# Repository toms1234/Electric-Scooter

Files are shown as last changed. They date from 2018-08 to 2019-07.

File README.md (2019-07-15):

# Electric-Scooter
////////////////////////////////////////////////////////////////////////////////////////////////////////////////////////////////////////
### TO-DO List
- [x] STAY UP TO DATE WITH THE COSTS OF THIS PROJECT
- [x] Add mathematics program output image (mathematics.jpg)
- [x] Add the Inventor Assembly as an image (design.gif & design.stl)
- [ ] Add an image of the mechanical part finished (mechanical.jpg)
- [ ] Add images of implemented safety (emergency stop & wiring in waterproof box = safety1.jpg & safety2.jpg)
- [ ] Add top speed in km/h and mph
- [ ] Add cost price
- [ ] Add logs (August 2018 up to ???)
- [ ] Add a complete image (final.jpg)
- [ ] Add a video demonstration (youtube video)
- [ ] Remove this list (everything in between the slashes)

////////////////////////////////////////////////////////////////////////////////////////////////////////////////////////////////////////


Top speed: ??? km/h ≈ ??? mph. [Video demonstration](http://www.youtube.com/watch?v=).

## The Idea
A design and practical implementation of a three-phase brushless DC (BLDC) motor control system for an electric scooter. 

My goal is to create an electric scooter that is powerful enough to pull me up hills while still keeping my own (and of course other road users) safety in mind. In this project I will address several possibilities to make the scooter safer.

The choices I made about the parts are discussed and compared with other possibilities.

The problems I faced during this project and how I fixed these problems are also discussed and explained. I also made a cost price of my scooter and compared it to current market offers of electric scooters.

## The Process
### 1. Risks
Some of the risks I thought of:
* Motor cannot be stopped
* Insufficient braking capacity
* Mass inertia
* Possible danger of understeer
* Too fast/estimation problem due to environment
* Too fast/estimation problem due to driver
* Not being able to warn other road users
* Accelerate too fast/decelerate too slowly
* Poor lighting
* Controller defective (throttle)
* Fall hazard due to driving with one hand
* Fall hazard due to not sitting on a saddle
* Risk of clamping of limbs/clothing
* Danger of slipping due to combination tire-road surface
* Explosion of the tires due to high speed
* Too large of a reaction time during braking
* Overheating of the motor
* Overheating the speedcontroller
* Possible dangers of the battery
* Short-circuit due to water intrusion/sudden temperature changes
* Slipping over footplate
* Hazards due to imbalance of the vehicle
* Uncontrollability during testing
* Roller chain fails

### 2. Mathematics
Took me less than 10 mins to write this simple mathematics program which will give me an easier time choosing a gear ratio:
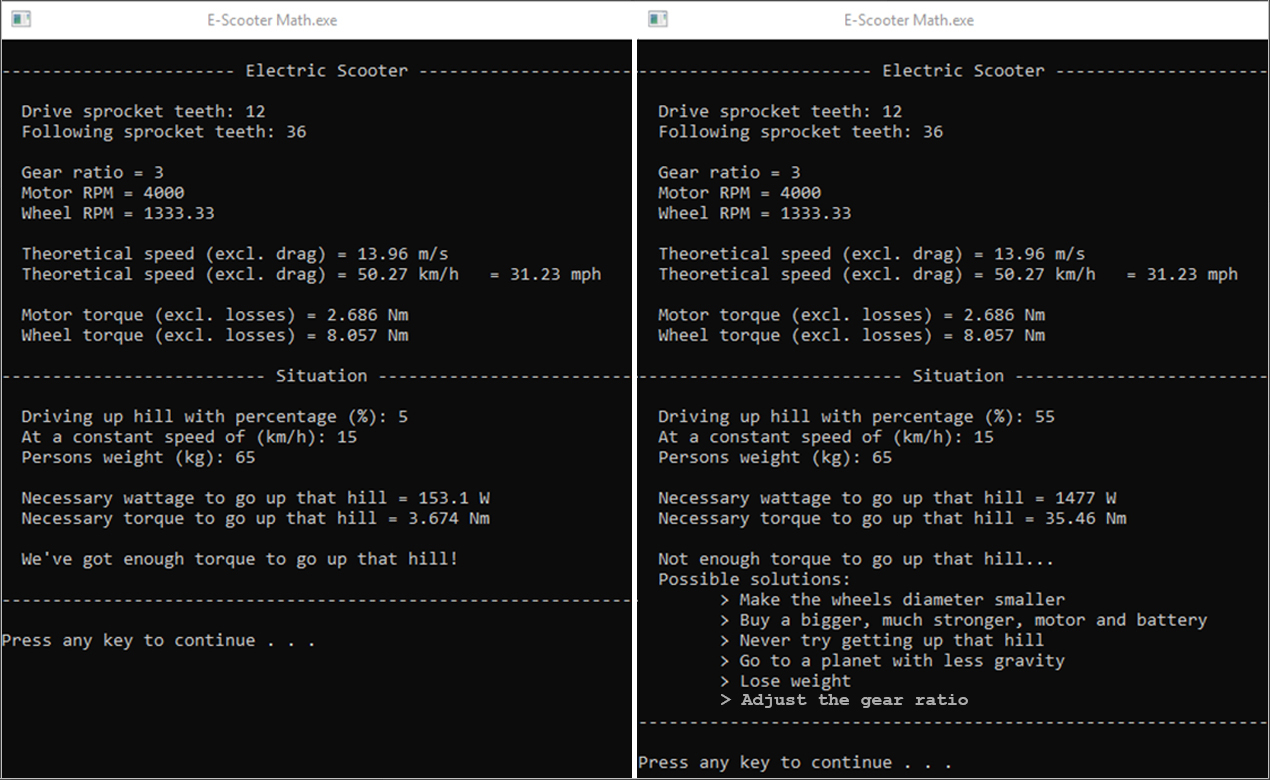
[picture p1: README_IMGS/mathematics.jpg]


The code is in the source. I later realised I could've simply used Excel...

As seen in the above (left) console output a gear ratio of 12 to 36 would do fine. I chose to go with the following parts:
* Drive sprocket (12 tooth 3/8“ x 7/32“ DIN ISO 606)
* Driven sprocket (36 tooth 3/8“ x 7/32“ DIN ISO 606)
* Roller chain (3/8“ x 7/32“ DIN ISO 606)

### 3. Design
I'm designing a completely new scooter frame, based of casual scooters with the motor driving the rear wheel.



Main electronics. These will go inside the waterproof box:
* Turnigy Aerodrive SK3 - 6374-149KV Brushless Outrunner Motor
* YEP 120A HV (4~14S) Brushless Speed Controller (OPTO)
* ZIPPY Compact 5000mAh 6S 25C Lipo Pack
* Arduino Uno V3

I chose to go with the above electronic components simply because I had already bought these for my [electric bike](https://github.com/rubenvanopstal/Electric-Bike) which I had disassembled before starting this project.

### 4. Production
Processes used to fabricate the scooter:
* Welding
* Milling
* Turning
* Boring
* Tapping



### 5. Software
First code, needs safety implementation:
```C++
#include <Servo.h>
Servo esc;

int throttlePin = 0;
 
void setup(){
  esc.attach(8);
}
 
void loop(){
  int throttle = analogRead(throttlePin);
  throttle = map(throttle, 0, 1023, 0, 179);
  esc.write(throttle);
}
```

### 6. Safety
Applying safety by thinking back on the risks I talked about. Changing software/hardware:
* Added a waterproof box (Short-circuit due to water intrusion/sudden temperature changes)
* Added an emergency stop (Motor cannot be stopped)
* Added a main switch
* Added fuses




* Added ramping in my code (Accelerate too fast/decelerate too slowly)
```C++
#include <Servo.h>
Servo esc;

#define throttlePin A0

#define MIN_READ_VALUE 178
#define MAX_READ_VALUE 880
#define MAX_SETPOINT 700
#define MAX_PWM 180

float throttleValue, throttleSafe, speed_diff, acceleration, setpoint, pwmCalc;

void setup() {
  pinMode(throttlePin, INPUT);
  esc.attach(8);
}

void loop() {  
  throttleValue = analogRead(throttlePin);
  if ((throttleValue > (MIN_READ_VALUE - 60)) && (throttleValue < (MAX_READ_VALUE + 20)))
  {    
    setpoint = throttleValue - 176;
    if (abs(setpoint) < 4) {
      setpoint = 0;
    } else if (abs(setpoint) > 695) {
      setpoint = 695;
    }

    throttleSafe = (setpoint * MAX_PWM)/MAX_SETPOINT;
    speed_diff = setpoint - pwmCalc;

    if (speed_diff > 2) {
      acceleration += 2;
      delay(50);
    }
    if (speed_diff < -2) {
      acceleration -= 2;
    }
    if (acceleration > 178) {
      acceleration = 178;
    }
    if (acceleration < 0) {
      acceleration = 0;
    }
    
    pwmCalc = (acceleration * MAX_SETPOINT)/MAX_PWM;
    esc.write(acceleration);
  }
  else if (throttleValue < (MIN_READ_VALUE - 80))
  {
    esc.write(0);
  }
  else if (throttleValue > (MAX_READ_VALUE + 40))
  {
    esc.write(0);
  }
  
}
```

### 7. Pricing
Cost: **€ ???**
* Motor
* Speedcontroller
* Programming card
* Batteries (5S & 6S LiPo)
* LiPo Balance charger
* Scooter wheels (200mm x 50mm = 8“)
* Sprockets (12 tooth & 36 tooth 3/8“ x 7/32“ DIN ISO 606)
* Roller chain (3/8“ x 7/32“ DIN ISO 606)
* Translock/taperlock (8mm x 19mm)
* Steel for the frame
* Waterproof box
* Heat shrink tubing
* All sorts of connectors
* Fuses & fuse holder
* Main switch
* Cables

Expenses I didn't take into account:
* Cutting plates from the milling and turning process
* Welding wire, power consumption and gas consumption from the welding process
* Power consumption of the milling machine and lathe
* DC-to-DC step-down converter, wires, soldering, small fuse, resistors, ...

### 8. Logs
August 2018 up to ?????.

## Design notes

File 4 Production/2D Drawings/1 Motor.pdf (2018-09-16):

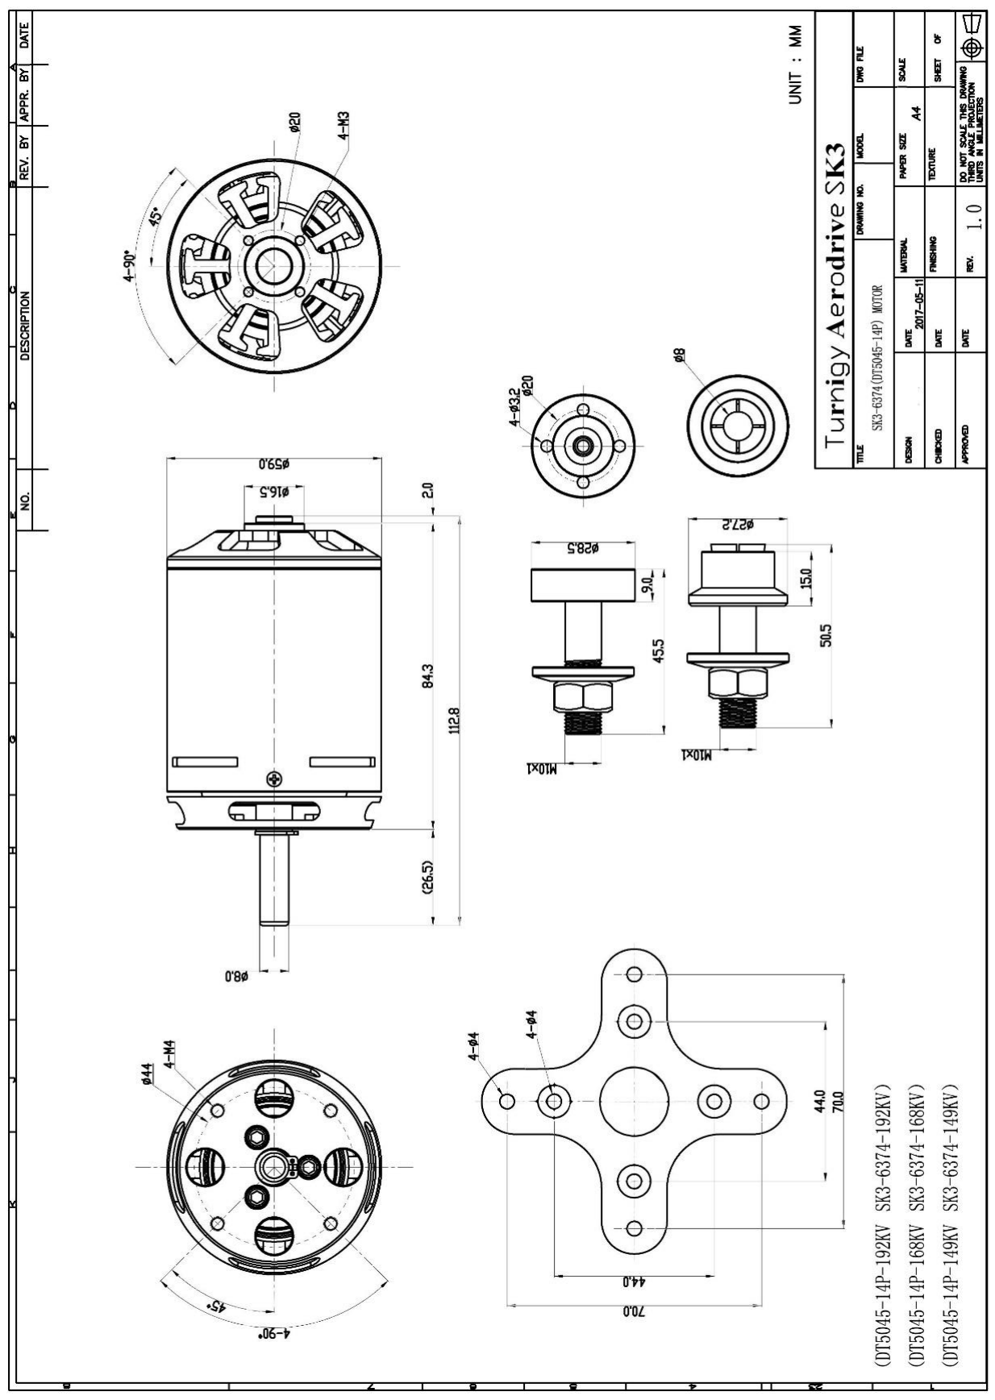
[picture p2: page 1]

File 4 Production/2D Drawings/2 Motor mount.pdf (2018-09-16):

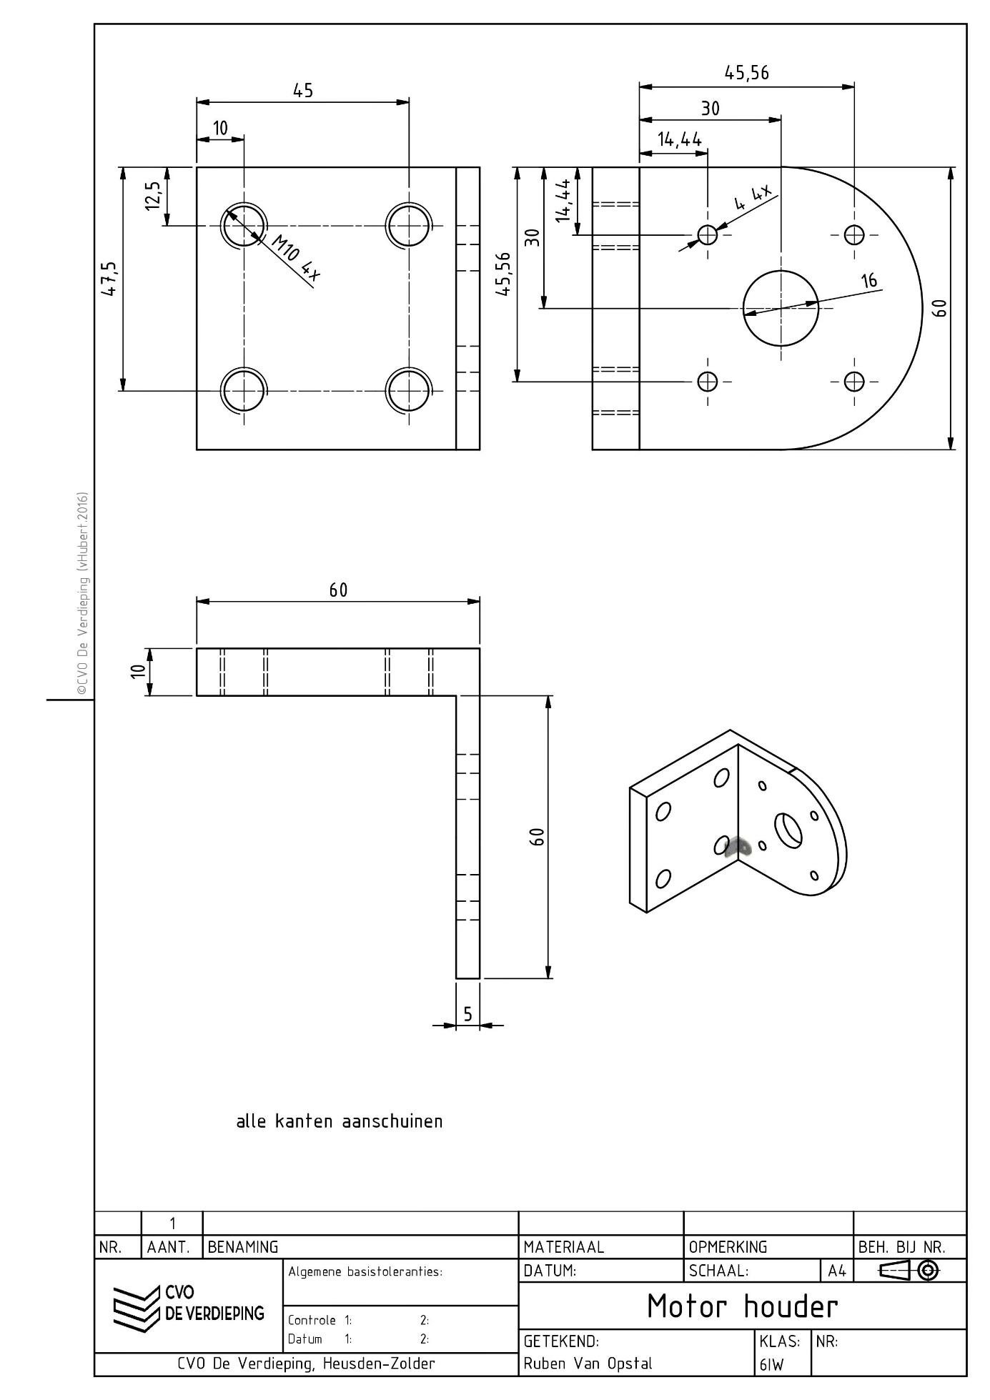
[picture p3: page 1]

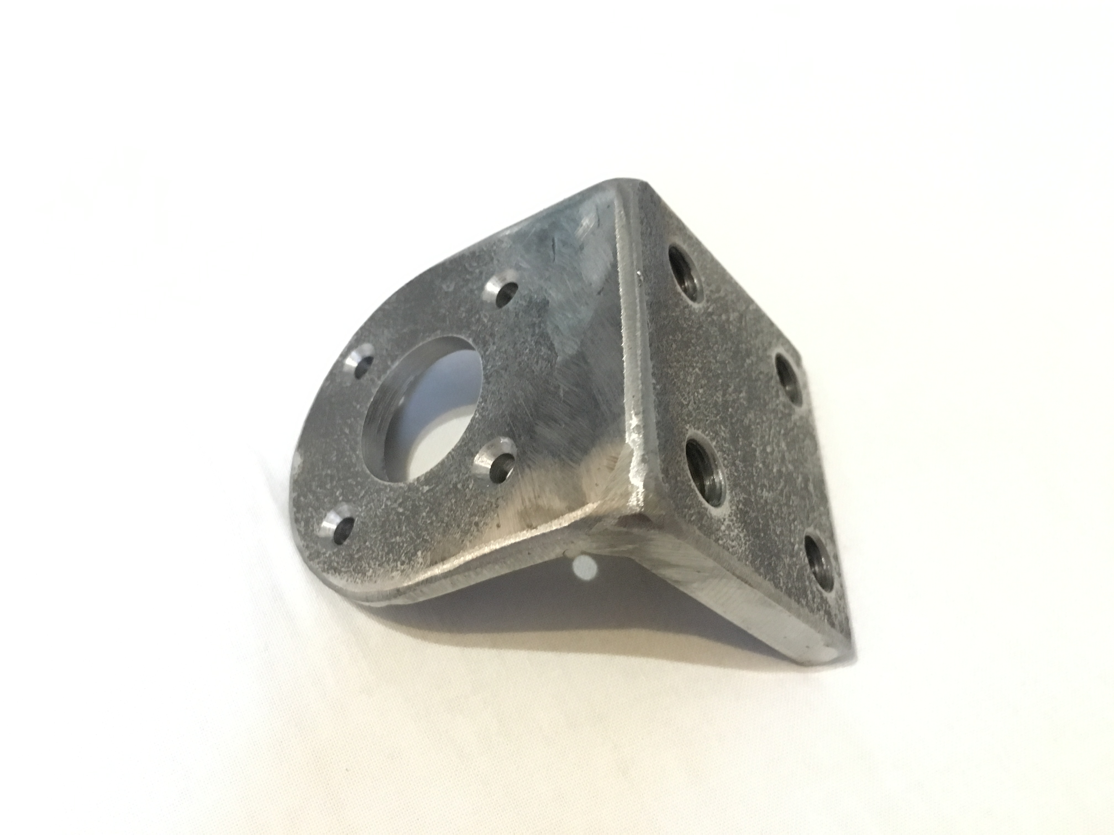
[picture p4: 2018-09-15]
4 Production/Pictures/3 Motor mount.JPG

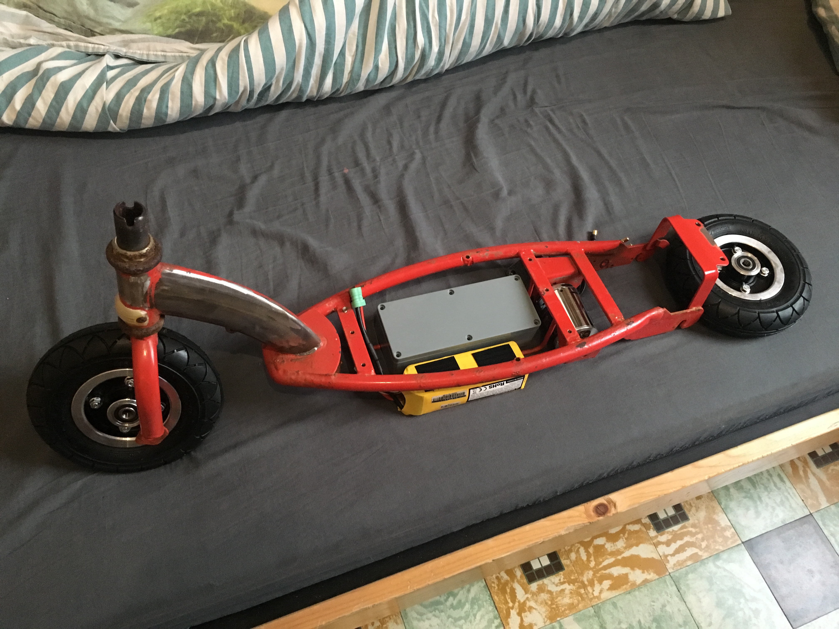
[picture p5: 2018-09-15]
4 Production/Pictures/1 Main idea.JPG

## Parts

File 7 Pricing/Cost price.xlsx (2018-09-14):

Cost price
Component | Type | Quantity | €/piece | Total
Electronics
Connectors | Team Corally - Bullit plug 6.5mm - Male | 2 | 6.50 | 13.00
Connectors | Team Corally - Bullit plug 6.5mm - Female | 2 | 6.50 | 13.00
Cables | Team Corally - Ultra V - Black and Red - 10AWG - ODø 5.5mm - 2x 1m | 2 | 19.95 | 39.90
Motor | Turnigy Aerodrive SK3 - 6374-149KV Brushless Outrunner Motor | 1 | 69.07 | 69.07
Speedcontroller | HobbyKing YEP 120A HV (4 ~ 14S) Brushless Speed Controller (OPTO) | 1 | 107.76 | 107.76
Programming card | YEP ESC Programming Card | 1 | 5.48 | 5.48
Battery | ZIPPY Compact 5000mAh 5S 25C Lipo Pack | 1 | 41.09 | 41.09
Battery | ZIPPY Compact 5000mAh 6S 25C Lipo Pack | 1 | 46.35 | 46.35
Battery charger | IMAX B6AC V2 Professional Balance Charger/Discharger | 1 | 38.19 | 38.19
Transmission
Sprocket | 12 tooth - 3/8“ x 7/32“ DIN ISO 606 | 2 | 2.93 | 5.86
Sprocket | 36 tooth - 3/8“ x 7/32“ DIN ISO 606 | 1 | 13.20 | 13.20
Roller chain | 3/8“ x 7/32“ DIN ISO 606 - 1m | 5 | 14.43 | 72.15
Connecting link | 3/8“ x 7/32“ DIN 8187 | 5 | 2.28 | 11.40
Taperlock | Translock® Mini - TRMINI8X19 - 8mm bore | 1 | 12.25 | 12.25
Wheels /w rims | 8“ - 200 x 50mm - Scoot wheels - Aluminium rims | 2 | 20.49 | 40.98
Aluminium / steel
 |  | 1 | 0.00 | 0.00
 |  | 1 | 0.00 | 0.00
 |  | 1 | 0.00 | 0.00
 |  | 1 | 0.00 | 0.00
 |  | 1 | 0.00 | 0.00
Safety
Case / box | Waterproof ABS box - Dark grey - 195 x 80 x 55mm G353 | 1 | 24.43 | 24.43
Cable shoes | Ring cable shoes - YELLOW - 6mm^2 - Diameter 8.4mm | 1 | 2.75 | 2.75
Cable shoes | Ring cable shoes - YELLOW - 6mm^2 - Diameter 6.4mm | 1 | 2.59 | 2.59
Fuse holder | Fuse holder for maxiOTO fuses | 1 | 11.39 | 11.39
Fuses | Blister maxiOTO fuses | 1 | 8.41 | 8.41
Main witch | Main switch 500A | 1 | 10.38 | 10.38
Griptape | SK8DLX Griptape | 1 | FREE | FREE
Totale kostprijs (€) | 589.63

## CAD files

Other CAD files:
3 Design/!Library/76229192-9-roulement_6000_2/OldVersions/roulement_6000_2.0003.iam
3 Design/!Library/76229192-9-roulement_6000_2/OldVersions/roulement_6000_2_01.0001.ipt
3 Design/!Library/76229192-9-roulement_6000_2/OldVersions/roulement_6000_2_02.0001.ipt
3 Design/!Library/76229192-9-roulement_6000_2/OldVersions/roulement_6000_2_03.0001.ipt
3 Design/!Library/76229192-9-roulement_6000_2/roulement_6000_2.iam
3 Design/!Library/76229192-9-roulement_6000_2/roulement_6000_2_01.ipt
3 Design/!Library/76229192-9-roulement_6000_2/roulement_6000_2_02.ipt
3 Design/!Library/76229192-9-roulement_6000_2/roulement_6000_2_03.ipt
3 Design/Electric-Scooter.iam
3 Design/Frame/Batterybox 1/Batterybox 1.ipt
3 Design/Frame/Batterybox 1/Waterproof box 1.ipt
3 Design/Frame/Batterybox 2/Batterybox 2.ipt
3 Design/Frame/Batterybox 2/OldVersions/Waterproof box 2.0008.ipt
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

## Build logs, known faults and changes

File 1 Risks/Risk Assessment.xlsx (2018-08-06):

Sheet: Revisie overzicht
Risico Analyse ombouwen tot electrisch aangedreven fiets
Revisie nummer | Omschrijving van de wijzigingen | Opgemaakt door / aanwezig tijdens meeting
1 | Opstart risico analyse, definitie, invullen, | Ruben Van Opstal / Maarten Wouters / Noach Van Opstal

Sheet: Risico Analyse
Risico Assessment Electric-Scooter
 | Risico Assessment |  | Evalution |  |  |  | Precautions and control measures
 | Actions of the involved people | Nature and description of the risks / problems | P | E | S | R | Source approach | Collective protection | Personal protection | Education | Instructions | Medical checkup | Other
item | Normal proceedings |  |  |  |  |  | Normal proceedings
1 | Motor cannot be stopped | Fall hazard, possible accident with other road users | 3 | 10 | 15 | 450 | Emergency stop | Warn bystanders | Protective clothing |  | Instruction card |  | Annual inspection of the complete vehicle by an authorized person with the necessary training
2 | Insufficient braking capacity | Not being able to stop in time, longer braking distance, swerve still possible | 1 | 6 | 7 | 42 | Better brakes or brake discs | Warn bystanders | Protective clothing
3 | Mass inertia | Heavier vehicle --> possible estimation problem with brakes | 6 | 10 | 15 | 900 |  |  | Protective clothing | Gain experience on private property | Instruction card
4 | Possible danger of understeer | By the electric drive relative to an ordinary vehicle | 0.5 | 3 | 3 | 4.5 |  |  | Protective clothing | Gain experience on private property | Instruction card
5 | Too fast / estimation problem due to environment | Danger to other road users | 3 | 6 | 7 | 126 | Limiter |  |  | Gain experience on private property
6 | Too fast / estimation problem due to driver | Danger to other road users + own danger | 6 | 10 | 15 | 900 | Limiter |  | Protective clothing | Gain experience on private property | Instruction card
7 | Not being able to warn other road users | Poor audible hearing possible by bystanders | 6 | 2 | 1 | 12 | A horn that mees certain conditions
8 | Accelerate too fast / decelrate too slowly | Lost vehicle control | 10 | 10 | 3 | 300 | Limiter |  | Protective clothing | Gain experience on private property | Instruction card
9 | Poor lighting | Invisible to other road users | 6 | 3 | 3 | 54 | Better lighting
10 | Controller defective (throttle) | Fall hazard, possible accident with other road users | 6 | 10 | 15 | 900 | Emergency stop |  | Protective clothing |  | Instruction card
11 | Fall hazard due to driving with one hand | Own danger | 3 | 1 | 7 | 21 | Manual, sensor that requires you to keep both hands on the handle bars |  | Protective clothing |  | Instruction card
12 | Fall hazard due to not sitting on a saddle | Own danger | 0.5 | 1 | 7 | 3.5 | Manual, add a saddle, sensor that requires you to sit on the saddle |  | Protective clothing |  | Instruction card
14 | Risk of clamping of limbs / clothing | Own danger | 6 | 10 | 7 | 420 | Hide objects with a pinch hazard |  | Protective clothing |  | Instruction card
15 | Danger of slipping due to combination tire-road surface | Lost vehicle control | 3 | 3 | 7 | 63 |  |  | Protective clothing | Gain experience on private property | Instruction card
16 | Explosion of tyres due to high speed | Lost vehicle control | 0.5 | 3 | 7 | 10.5 | Emergency stop, limiter |  | Protective clothing |  | Instruction card
18 | Too long of a reaction time during breaking | Danger to other road users + own danger | 6 | 10 | 3 | 180 |  | Warn bystanders | Protective clothing | Gain experience on private property | Instruction card
19 | Overheating of the motor | Technical failure of the vehicle | 0.5 | 10 | 1 | 5 | Cooling of the engine |  |  |  | Instruction card
20 | Overheating of the speedcontroller | Technical failure of the vehicle | 0.5 | 10 | 1 | 5 | Cooling of the speedcontroller |  |  |  | Instruction card
21 | Possible dangers of the battery | Explosion hazard, flammable | 3 | 6 | 1 | 18 | Protect the battery |  |  |  | Instruction card
22 | Short-circuit due to water intrusion / sudden temperature changes | Technical failure of the vehicle | 3 | 6 | 1 | 18 | Waterproofing of components |  |  |  | Instruction card
23 | Slipping over footplate | Fall hazard, possible accident with other road users | 3 | 1 | 1 | 3 | Griptape |  | Protective clothing
24 | Hazards due to imbalance of the vehicle | Fall hazard, possible accident with other road users | 10 | 10 | 3 | 300 | Counterweight |  | Protective clothing |  | Instruction card
25 | Roller chain fails | Technical failure of the vehicle | 0.2 | 10 | 1 | 2
27 | Uncontrollability during testing | Lost vehicle control | 10 | 10 | 15 | 1500 | Emergency stop | Testing in a controlled environment | Protective clothing | Gain experience on private property

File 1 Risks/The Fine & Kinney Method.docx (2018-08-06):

The Fine & Kinney Method
Probability (mathematical chance an incident will occur) | | | P
To be expected | | | 10
Possible | | | 6
Unusual (but possible) | | | 3
Unlikely, but possible in the long term | | | 1
Highly unlikely, but conceivable | | | 0,5
Almost unimaginable | | | 0,2
Next to impossible / unthinkable | | | 0,1
Exposure (duration that a risk can occur) | | | E
Constantly | 20-40 hrs/week (constantly) | | 10
Frequently | 10-20 hrs/week (1x/day) | | 6
Occasionally | 5-10 hrs/week (1x/week) | | 3
Sometimes | 2-5 hrs/week (1x/month) | | 2
Rarely | 10min-2hrs/week (2-3x/year) | | 1
Very rarely | < 10min/week. (1x/year) | | 0,5
Severity (possible damage, effects and consequences) | | | S
Disaster | Multiple dead people | | 100
Catastrophe | One or more dead people | | 40
Very severe | Fatal casualty | | 15
Severe | Lasting injury with absence | | 7
Important | Injury with absence (> several days but < months) | | 3
Slight effect | Injury without absence through illness | | 1
Risk-index (R) | Priority (P) | Risk = P * E * S
> 400 | 1 | Risk is too high; stop activities / operations
201-400 | 2 | High risk; apply large measures immediately
71-200 | 3 | Moderate risk; apply simple measures
21-70 | 4 | Little risk; attention required
0-20 | 5 | Slight risk; acceptable

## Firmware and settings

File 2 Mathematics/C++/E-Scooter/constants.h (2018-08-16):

#pragma once

#define M_PI 3.14159265358979323846264338327950288

const double batteryVolt = (6 * ((4.2 + 3.7) / 2));
const int motorRPM = 4000;		// at half voltage = 6S
const int motorWatt = 1125;		// watts

const double wheelDia = 0.2;	// meters

const double kmh_mph_ratio = 0.6213712;

const double gravity = 9.81;		// m/s^2
const double scooterWeight = 10;	// kg

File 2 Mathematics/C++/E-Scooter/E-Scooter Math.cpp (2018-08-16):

// Electric-Scooter-Mathematics.cpp : Defines the entry point for the console application.
//

#include "stdafx.h"
#include <iostream>
#include <iomanip>
#include <math.h>

int getInteger()
{
	while (true)
	{
		int x;
		std::cin >> x;
		std::cin.ignore(32767, '\n');

		if (std::cin.fail())
		{
			std::cin.clear();
			std::cin.ignore(32767, '\n');
		}
		else
			return x;
	}
}

double getDouble()
{
	while (true)
	{
		double x;
		std::cin >> x;
		std::cin.ignore(32767, '\n');

		if (std::cin.fail())
		{
			std::cin.clear();
			std::cin.ignore(32767, '\n');
		}
		else
			return x;
	}
}

int main()
{
	std::cout << "\n----------------------- Electric Scooter ----------------------\n" << std::endl;

	std::cout << "  Drive sprocket teeth: ";
	int driveTooth = getInteger();

	std::cout << "  Driven sprocket teeth: ";
	int followTooth = getInteger();

	float gearRatio = static_cast<float>(followTooth) / driveTooth;
	std::cout << std::setprecision(6);
	std::cout << "\n  Gear ratio = " << gearRatio << std::endl;
	std::cout << "  Motor RPM = " << motorRPM << std::endl;

	double wheelRPM = motorRPM / gearRatio;
	std::cout << "  Wheel RPM = " << wheelRPM << std::endl;

	std::cout << std::setprecision(4);

	double speedMS = (M_PI * wheelDia * wheelRPM) / 60;
	std::cout << "\n  Theoretical speed (excl. drag) = " << speedMS << " m/s" << std::endl;

	double speedKMH = speedMS * 3.6;
	std::cout << "  Theoretical speed (excl. drag) = " << speedKMH << " km/h" << "\t= " << speedKMH * kmh_mph_ratio << " mph" << std::endl;

	double motorTorque = motorWatt / ((2 * M_PI * motorRPM) / 60);
	std::cout << "\n  Motor torque (excl. losses) = " << motorTorque << " Nm" << std::endl;

	double wheelTorque = motorTorque * gearRatio;
	std::cout << "  Wheel torque (excl. losses) = " << wheelTorque << " Nm" << std::endl;

	std::cout << "\n-------------------------- Situation --------------------------\n" << std::endl;

	std::cout << std::resetiosflags(std::ios::fixed | std::ios::showpoint);

	{
		std::cout << "  Driving up hill with percentage (%): ";
		double percentage = getDouble();
		std::cout << "  At a constant speed of (km/h): ";
		double velocity = getDouble();
		std::cout << "  Persons weight (kg): ";
		double personWeight = getDouble();
		double mass = personWeight + scooterWeight;

		double necessaryWatt = mass * gravity * sin(atan(percentage / 100)) * (velocity / 3.6);
		std::cout << "\n  Necessary wattage to go up that hill = " << necessaryWatt << " W" << std::endl;

		double necessaryTorque = mass * gravity * sin(atan(percentage / 100)) * (wheelDia / 2);
		std::cout << "  Necessary torque to go up that hill = " << necessaryTorque << " Nm" << std::endl;

		if (wheelTorque > necessaryTorque)
			std::cout << "\n  We've got enough torque to go up that hill!\n" << std::endl;
		else {
			std::cout << "\n  Not enough torque to go up that hill..." << std::endl;
			std::cout << "  Possible solutions:" << std::endl;
			std::cout << "\t> Adjust the gear ratio" << std::endl;
			std::cout << "\t> Make the wheels diameter smaller" << std::endl;
			std::cout << "\t> Buy a bigger, much stronger, motor and battery" << std::endl;
			std::cout << "\t> Never try getting up that hill" << std::endl;
			std::cout << "\t> Go to a planet with less gravity" << std::endl;
			std::cout << "\t> Lose weight\n" << std::endl;
		}

		std::cout << "---------------------------------------------------------------\n" << std::endl;
	}

	system("pause");
	return 0;
}

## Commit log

2018-08-10 Revert "Add files via upload"
    This reverts commit 00b28823fc4d59c66b59f784d59acb86ae5609cc.
    [roulement_6000_2.0003.iam, roulement_6000_2.iam, roulement_6000_2_01.0001.ipt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]
2018-09-14 Update Cost price.xlsx
    [Cost price.xlsx]
2018-09-16 Add 2D Drawings of motor
2018-10-11 Revert "Add Python version"
    This reverts commit bd46e36bbeddf4a0f9a531f2061b9d87c0cda01b.
    [E-Scooter Math.cpp, constants.h]
